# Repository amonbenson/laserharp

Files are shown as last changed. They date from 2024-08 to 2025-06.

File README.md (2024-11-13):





## Development Setup

### Backend

Setup a virtual environment and install the dependencies:
```bash
python3 -m venv .venv --system-site-packages
source .venv/bin/activate
pip install -r requirements.txt
```

Run the server in development mode:
```bash
source .venv/bin/activate
python -m laserharp.server
```

### Frontend

Install node js and yarn:
```bash
wget -qO- https://raw.githubusercontent.com/nvm-sh/nvm/v0.40.1/install.sh | bash
nvm install --lts
nvm use --lts
npm install -g yarn
```

Install all dependencies:
```bash
cd frontend
yarn install
```

Run the development server:
```bash
yarn dev
```

## Raspberry Pi Performance Improvements:

see https://wiki.linuxaudio.org/wiki/raspberrypi

```bash
for cpu in /sys/devices/system/cpu/cpu[0-9]*; do echo -n performance \
| sudo tee $cpu/cpufreq/scaling_governor; done
```

## Raspberry Pi Reduce Power Consumption

see https://www.jeffgeerling.com/blog/2023/reducing-raspberry-pi-5s-power-consumption-140x

```bash
# sudo rpi-eeprom-config -e
[all]
BOOT_UART=1
WAKE_ON_GPIO=0
POWER_OFF_ON_HALT=1
```

## Midi uart
- do a `rpi-update` to get the latest kernel firmware
- add to `/boot/firmware/config.txt`:
```
dtoverlay=uart2-pi5
dtoverlay=midi-uart2-pi5
```

## Power via GPIO header
http://blog.dddac.com/wp-content/uploads/Flash-RPi5-and-adding-5000mA-Line-tutorial.pdf

## Allow current user to shutdown
```bash
sudo chmod u+s /sbin/poweroff /sbin/reboot /sbin/shutdown
```

## Diode to Note Mapping

- Root note: C3 (midi note 48, one octave below middle C)
- Global transpose setting

- Modes:
    - **Pedal Harp**: For each note, choose one of:
        - flat
        - natural
        - sharp
    - **Custom Scale**:
        - each diode can be assigned to a specific midi note

- The harp is divided into three horizontal sections resulting in 3 different octave ranges

## Transmitted MIDI Messages

:heavy_check_mark: &ndash; Implemented<br>
:x: &ndash; Not implemented

### Note On :heavy_check_mark:

```
Laserharp -> Host: 0x90 <note> <velocity>
```
Sent when a laser is intercepted. The note value is determined by the diode and section that was intercepted. The velocity is fixed at 127.

### Note Off :heavy_check_mark:

```
Laserharp -> Host: 0x80 <note> <velocity>
```

Sent immediately after a laser was plucked. The velocity is fixed at 127.

### Pitch Bend :x:

```
Laserharp -> Host: 0xe0 <pitch_bend_msb> <pitch_bend_lsb>
```

Sent during interception when the hand is moved along the laser beam.

## Received MIDI Messages

:heavy_check_mark: &ndash; Implemented<br>
:x: &ndash; Not implemented

### Set Laser Brightness Directly (Note On / Note Off) :heavy_check_mark: (set all lasers :x:)

```
Host -> Laserharp: 0x80 <note> <velocity>
```

Turn off the laser corresponding to the note. A note value of 127 will turn off all lasers at once.

```
Host -> Laserharp: 0x90 <note> <velocity>
```

Turn on the laser corresponding to the note. A note value of 127 will turn on all lasers at once. The velocity determines the brightness of the laser.

The brightness is restored automatically after 1s. Note that interceptions will not be detected when the laser is turned off or too dim.

### Restore Laser Brightness (CC 102) :heavy_check_mark:

```
Host -> Laserharp: 0xb0 102 <value>
```

Restores the laser brightness to the previous value immediately. Value must be &ge; 64.

### Set Unplucked Laser Brightness (CC 103) :heavy_check_mark:

```
Host -> Laserharp: 0xb0 103 <brightness>
```

Set the brightness for unplucked lasers.

### Set Plucked Laser Brightness (CC 104) :heavy_check_mark:

```
Host -> Laserharp: 0xb0 104 <brightness>
```

Set the brightness when a laser is plucked.

### Set Muted Laser Brightness (CC 105) :heavy_check_mark:

```
Host -> Laserharp: 0xb0 105 <brightness>
```

Sets the brightness when a laser is muted.

### Set Pedal Position And Mutes (CC 110 - 116) :heavy_check_mark:

```
Host -> Laserharp: 0xb0 <pedal_cc> <position>
```

Sets the position and mute of a pedal.
The pedals are mapped as follows:

- CC 110 &ndash; C pedal
- CC 111 &ndash; D pedal
- CC 112 &ndash; E pedal
- CC 113 &ndash; F pedal
- CC 114 &ndash; G pedal
- CC 115 &ndash; A pedal
- CC 116 &ndash; B pedal

The value is divided into the ranges:

- 0 &ndash; 31 &ndash; muted
- 32 &ndash; 63 &ndash; lower position (sharp)
- 64 &ndash; 95 &ndash; middle position (natural)
- 96 &ndash; 127 &ndash; upper position (flat)

## IPC Protocol

:heavy_check_mark: &ndash; Implemented<br>
:x: &ndash; Not implemented

### USB Midi :x:

```
Bidirectional: 0x0N <byte0> <byte1> <byte2>
```

These packets are equivalent to the USB Midi Protocol with `CN = 1`.

### Din Midi :x:

```
Bidirectional: 0x1N <byte0> <byte1> <byte2>
```

_Note: With the current version, Din Midi is handled directly by the Raspberry Pi, so this message won't be used._

These packets are equivalent to the USB Midi Protocol with `CN = 1`.

### Set Brightness of a Single Laser :heavy_check_mark:

```
RPi -> STM: 0x80 <diode_index> <brightness> <fade_duration>
```

Set the brightness of a single laser diode. The fade duration is given in tenths of a second. E.g. a value of 20 will fade the laser to the new brightness over 2 seconds. A duration of 0 will set the brightness immediately.

### Set Brightness of All Lasers :heavy_check_mark:

```
RPi -> STM: 0x81 <brightness> <fade_duration> <unused>
```

Set the brightness of all laser diodes. The fade duration is given in tenths of a second. E.g. a value of 20 will fade the lasers to the new brightness over 2 seconds. A duration of 0 will set the brightness immediately.

### Get Brightness of a Single Laser :heavy_check_mark:

```
RPi -> STM: 0x82 <diode_index> <unused> <unused>
STM -> RPi: 0x82 <diode_index> <brightness> <unused>
```

### Play Animation :heavy_check_mark:

```
RPi -> STM: 0x83 <animation_id> <duration> <follow_action>
```

Play one of the predefined animations.

**Animation Ids**:<br>
0 &ndash; **Boot animation** &ndash; Played during powerup of the Raspberry Pi<br>
1 &ndash; **Flip animation** &ndash; Played when flipping the harp view<br>
2 &ndash; **Test animation** &ndash; Used for internal testing, alternates between diodes 4 and 5

**Duration**: Given in tenths of a second. E.g. a value of 20 will play the animation for 2 seconds.

**Follow Actions**:<br>
0 &ndash; **Loop** &ndash; Loop the animation indefinitely<br>
1 &ndash; **Freeze** &ndash; Play the animation once and stop on the last frame<br>
2 &ndash; **Off** &ndash; Play the animation once and stop with all lasers off<br>
3 &ndash; **Restore** &ndash; Play the animation once and restore the laser brightnesses

### Stop Animation :heavy_check_mark:

```
RPi -> STM: 0x84 <unused> <unused> <unused>
```

Stop the current animation from playing and execute the follow action immediately. If the follow action was set to 0 (loop indefinitely), the animation will stop and the lasers will remain in their current state.

### Calibration Button Pressed :heavy_check_mark:

```
STM -> RPi: 0x90 <state_0> <state_1> <state_2>
```

Sent when the calibration button is pressed. The states are given as follows:
0 &ndash; released<br>
1 &ndash; short press<br>
2 &ndash; long press

For example, if the button is short-pressed, then long-pressed, and then released, the states will be `0x01 0x02 0x00`.

### Get Voltage :heavy_check_mark:

```
RPi -> STM: 0x91 <00> <unused> <unused>
STM -> RPi: 0x91 <00> <voltage_int> <voltage_frac>
```

Returns the current voltage. Currently only the Laser Diode voltage (index 0) can be measured. The result is given as a decimal number with a resolution of 0.01V and can be calculated as follows:

```python
voltage = voltage_int + voltage_frac / 100
```

### Firmware Version Inquiry :heavy_check_mark:

```
RPi -> STM: 0xf0 <unused> <unused> <unused>
STM -> RPi: 0xf0 <major> <minor> <patch>
```

### Reboot STM :heavy_check_mark:

```
RPi -> STM: 0xf1 <unused> <unused> <unused>
```

### Enter Standby :heavy_check_mark:

```
RPi -> STM: 0xf2 <fade_delay> <fade_duration> <unused>
```

Starts by playing the boot animation, waits for the fade delay, and then fades the lasers to black over the fade duration. Both delay and duration are given in tenths of a second.

**Important: This is intended to be used when the harp is turned off. It will block any further IPC commands and the STM will not respond until it is power cycled.**

## TODO Software

### Pedal Mutes

- Each Pedal Switch should have a "mute" button. If a string is muted, its corresponding laser will be turned on very dimly and no sound will be produced for that string.

### Direct Laser Control

- The brightness of each laser should be directly controllable via Note On Messages.
- Velocity 1 will map to 0% brightness, velocity 127 will map to 100% brightness.
- Velocity 0 / Note Off will return to normal operation and use the internally calculated laser brightness
- If a laser is currently in "normal operation" mode, the color will be determined by the "unplucked", "plucked", and "muted" brightness settings.

### Section Mode / Section Transpose (formally Section Octave Spacing)

- Sections can be set to different modes.
    - Off &ndash; There are no different sections. Each laser will produce a single note.
    - Alterate &ndash; The upper section will play one semitone higher while the lower section will play one semitone lower.
    - Single Octave &ndash; The upper section will play one octave higher while the lower section will play one octave lower.
    - Double Octave &ndash; The upper section will play two octaves higher while the lower section will play two octaves lower.
- Internally, the section mode is stored as a number of semitones.
- This should also be controllable via a Control Change Message

### Global Transpose

- Instead of setting the root note, a fixed root note (e.g. C3) will be used and a global transpose setting will offset that root note.

### Direct Pedal/Mute Control

- Using Control Change Messages, the pedal position and mutes can be controlled.

### Predefined Scales

- Each predefined scale controls the pedal positions and mutes for each note.
- Can be selected using Bank Change Messages (CC 0).
- Additional custom scales can be defined and stored internally.

- For each scale, choose:
    - Pitch: `C C# D D# E F F# G G# A A# B`
    - Modes (see https://en.wikipedia.org/wiki/List_of_musical_scales_and_modes):
        - Lydian Dominant &ndash; `1 2 3 #4 5 6 b7`

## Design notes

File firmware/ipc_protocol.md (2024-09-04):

## Uses USB Midi internally

CN 0: DIN
CN 1: USB
CN 2: BLE
CN 8: Laser Brightness (note 127 = set all)

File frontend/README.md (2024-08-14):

# laserharp

This template should help get you started developing with Vue 3 in Vite.

## Recommended IDE Setup

[VSCode](https://code.visualstudio.com/) + [Volar](https://marketplace.visualstudio.com/items?itemName=Vue.volar) (and disable Vetur).

## Customize configuration

See [Vite Configuration Reference](https://vitejs.dev/config/).

## Project Setup

```sh
npm install
```

### Compile and Hot-Reload for Development

```sh
npm run dev
```

### Compile and Minify for Production

```sh
npm run build
```

### Lint with [ESLint](https://eslint.org/)

```sh
npm run lint
```

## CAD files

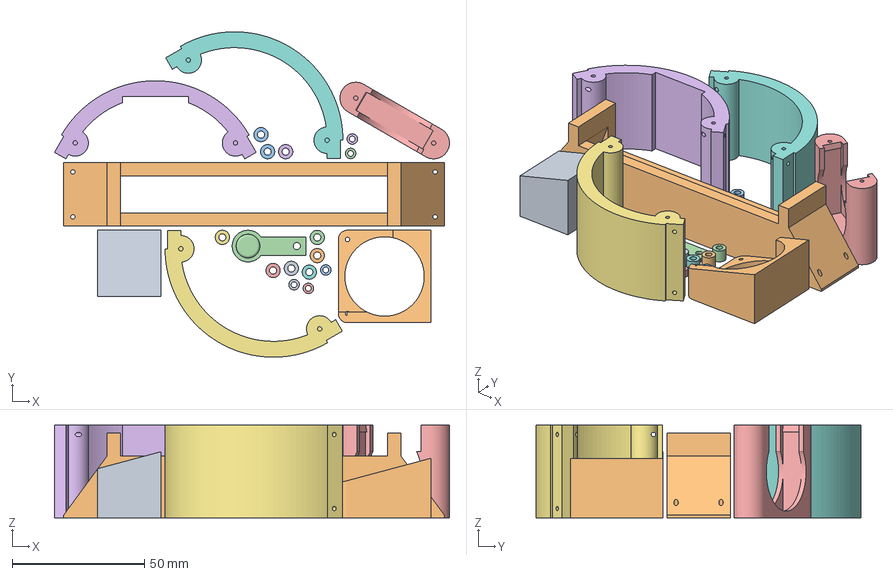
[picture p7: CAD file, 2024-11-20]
hardware/3dp/3dp_parts.3mf
149.4 x 123.1 x 35.0 mm
Small Spacer.3mf
Laser Cabinet.3mf
Large Spacer.3mf
Front Button.3mf
Fan Mount.3mf
Case Top.3mf
Case Right.3mf
Case Left.3mf
Camera Mount.3mf
Camera Cabinet.3mf
Large Spacer.3mf(1)
Large Spacer.3mf(2)
Large Spacer.3mf(3)
Large Spacer.3mf(4)
Large Spacer.3mf(5)
Large Spacer.3mf(6)
Large Spacer.3mf(7)
Large Spacer.3mf(8)
Small Spacer.3mf(1)
Small Spacer.3mf(2)
Small Spacer.3mf(3)
Small Spacer.3mf(4)

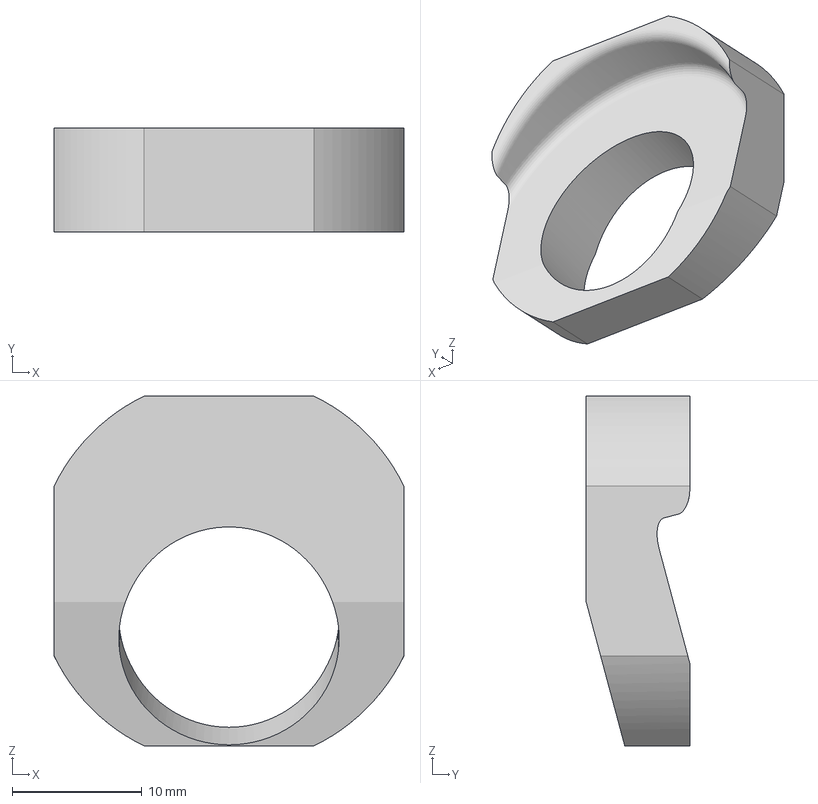
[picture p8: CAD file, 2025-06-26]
hardware/3dp/jlc3dp/LensMount.3mf
27.0 x 8.00 x 27.0 mm

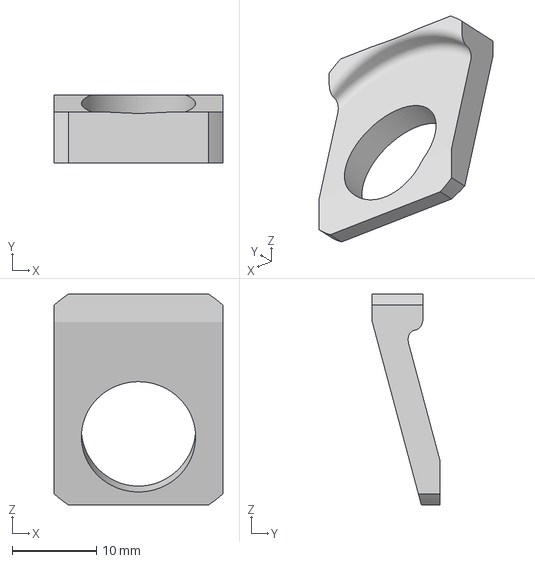
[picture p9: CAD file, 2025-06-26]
hardware/fusion360/Export/3D Printing/Lens Mount.3mf
20.0 x 8.00 x 25.0 mm

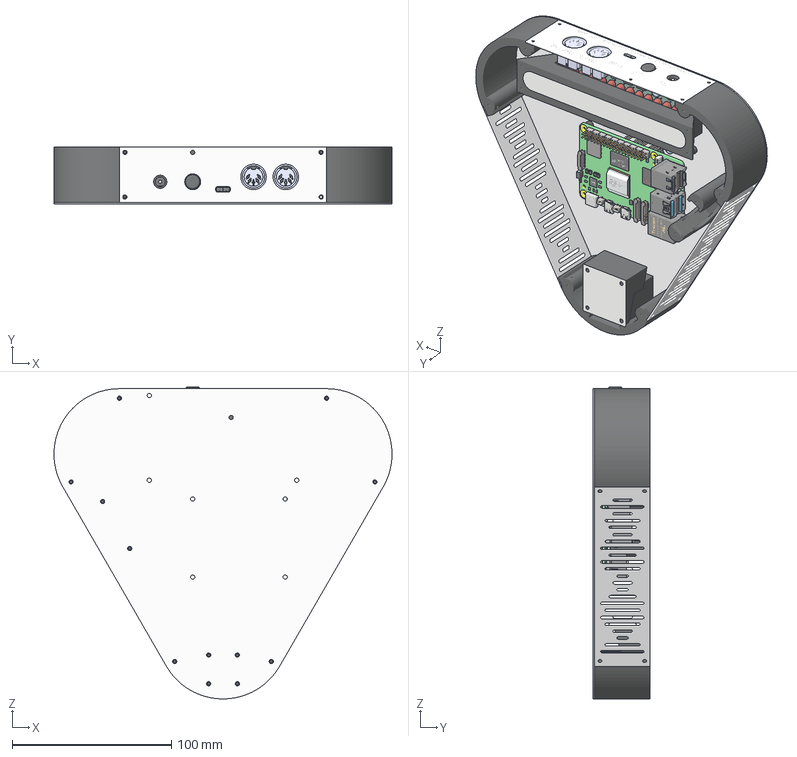
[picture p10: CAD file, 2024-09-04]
hardware/fusion360/Export/Laserharp Frameless 3DP Parts.3mf
212.0 x 36.0 x 195.6 mm
Bottom Plate
Camera Cabinet
Camera Cover
Camera Mount
Case Left
Case Right
Case Top
Fan Mount
Front Button
Front Plate
Laser Cabinet
Laser Cover
Left Side Panel
Right Side Panel
Spacer (1)
Spacer (10)
Spacer (11)
Spacer (2)
Spacer (3)
Spacer (4)
Spacer (5)
Spacer (6)
Spacer (7)
Spacer (8)
Spacer (9)
Spacer

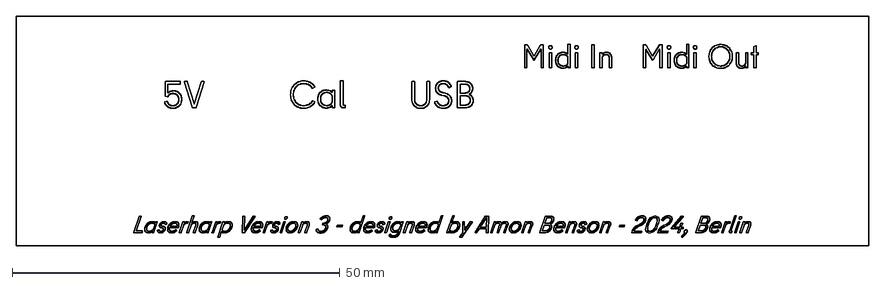
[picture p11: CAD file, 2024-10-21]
hardware/fusion360/Export/Sheet Metal/Engravings.dxf
130.0 x 35.0 mm

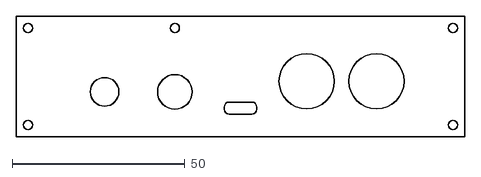
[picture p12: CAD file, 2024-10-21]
hardware/fusion360/Export/Sheet Metal/Fabrication/LH_Front_Outlines.dxf
130.0 x 35.0

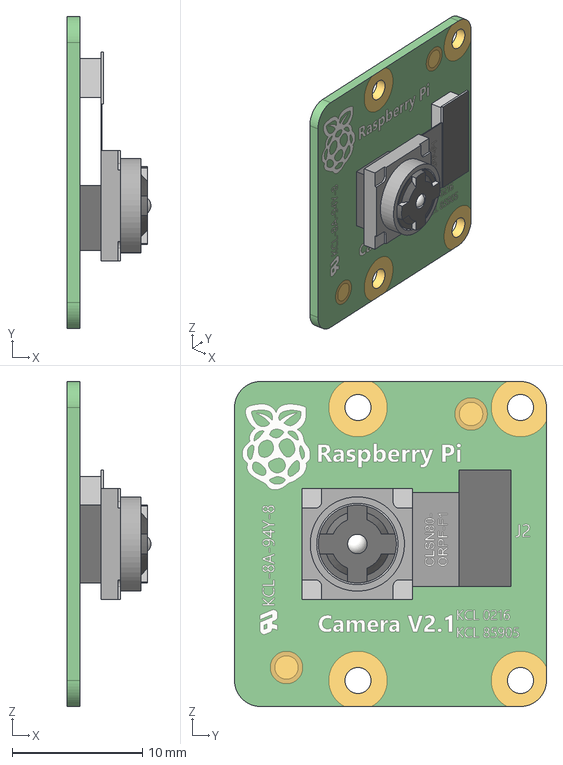
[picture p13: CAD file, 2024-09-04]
hardware/fusion360/PCB Models/Cam V2.1 v1.step
6.45 x 24.0 x 25.0 mm

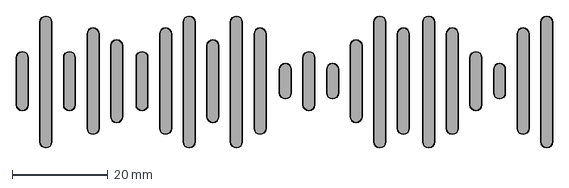
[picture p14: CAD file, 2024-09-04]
hardware/waveform_artwork.dxf
112.2 x 27.5 mm

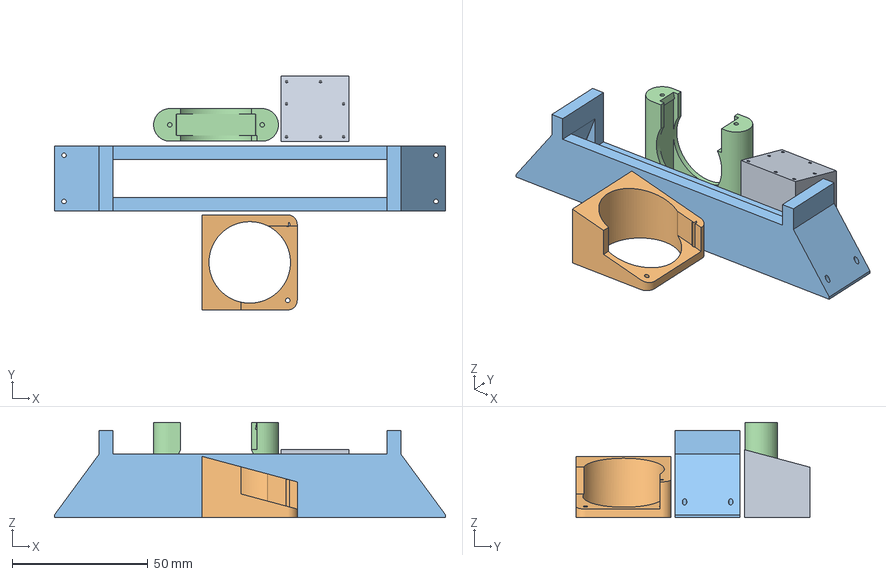
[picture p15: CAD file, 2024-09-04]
hardware/3dp/Cura_Mounts.3mf
144.0 x 86.1 x 35.0 mm
Camera Mount.3mf
Camera Cabinet.3mf
Laser Cabinet.3mf
Fan Mount.3mf

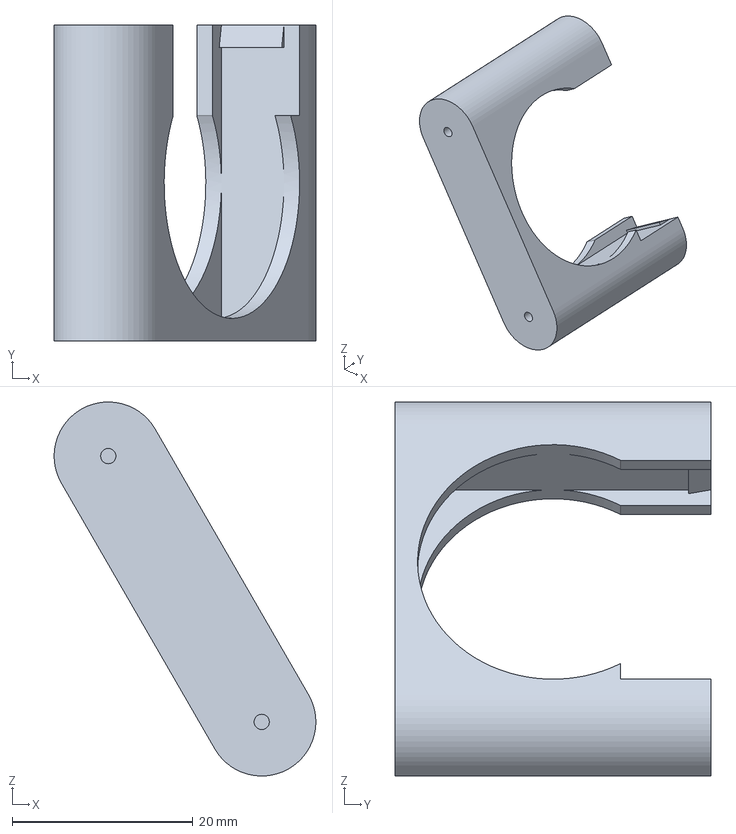
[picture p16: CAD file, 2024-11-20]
hardware/3dp/jlc3dp/FanMount.3mf
29.0 x 35.0 x 41.4 mm

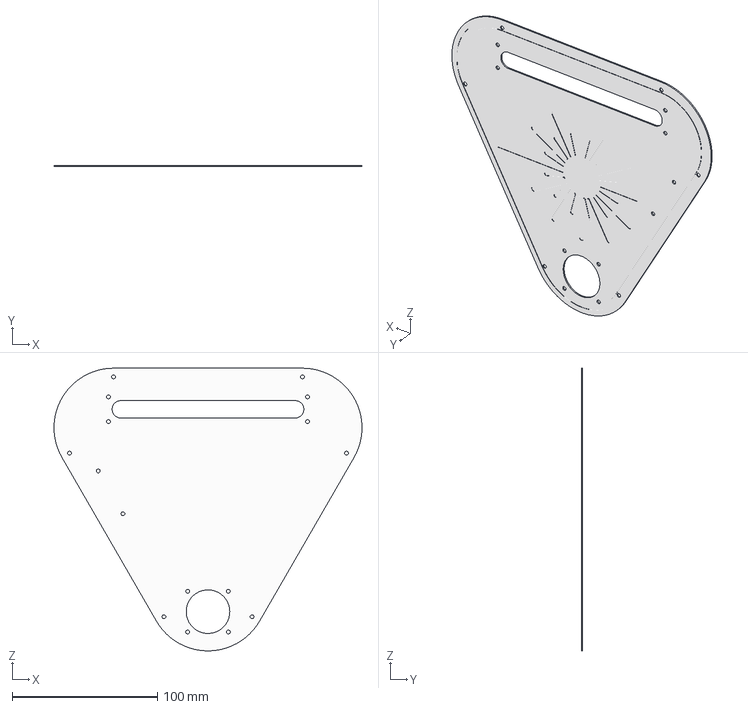
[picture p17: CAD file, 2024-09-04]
hardware/fusion360/Export/3D Printing/Top Plate.3mf
212.0 x 1.00 x 194.5 mm

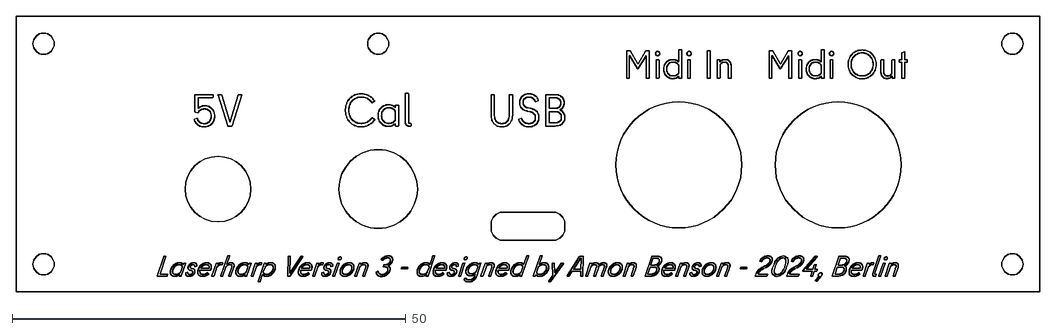
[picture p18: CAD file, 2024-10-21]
hardware/fusion360/Export/Sheet Metal/Fabrication/LH_Front.dxf
130.0 x 35.0

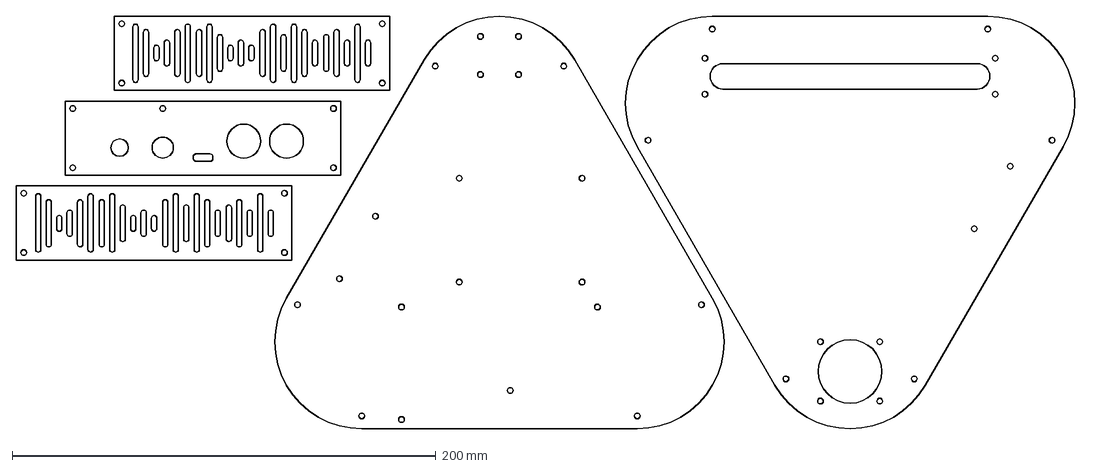
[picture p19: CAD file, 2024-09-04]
hardware/fusion360/Export/Sheet Metal/Outlines.dxf
501.2 x 194.6 mm

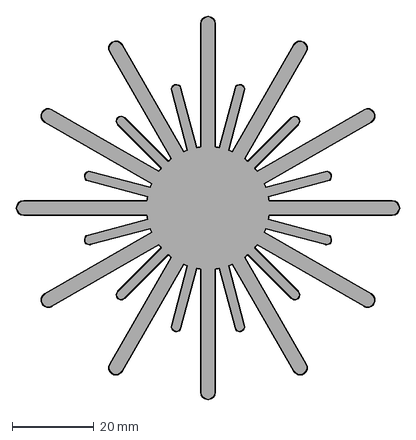
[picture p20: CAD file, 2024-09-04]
hardware/laser_artwork.dxf
93.5 x 93.5 mm

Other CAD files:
hardware/3dp/Cura_Top_Plate.3mf
hardware/3dp/jlc3dp/CameraCabinet.3mf
hardware/fusion360/Export/3D Printing/Front Button.3mf
hardware/fusion360/Export/Sheet Metal/Fabrication/LH_Left.dxf
hardware/3dp/Cura_Bottom_Plate.3mf
hardware/3dp/Cura_Case_And_Button.3mf
hardware/3dp/Cura_Panels.3mf
hardware/3dp/Cura_Spacers.3mf
hardware/3dp/jlc3dp/CameraMount.3mf
hardware/3dp/jlc3dp/CaseLR_x2.3mf
hardware/3dp/jlc3dp/CaseTop.3mf
hardware/3dp/jlc3dp/FrontButton.3mf
hardware/3dp/jlc3dp/LargeSpacer_x9.3mf
hardware/3dp/jlc3dp/LaserCabinet.3mf
hardware/3dp/jlc3dp/SmallSpacer_x5.3mf
hardware/Top Plate.dxf
hardware/fusion360/Export/3D Printing/Bottom Plate.3mf
hardware/fusion360/Export/3D Printing/Camera Cabinet.3mf
hardware/fusion360/Export/3D Printing/Camera Mount.3mf
hardware/fusion360/Export/3D Printing/Case Left.3mf
hardware/fusion360/Export/3D Printing/Case Right.3mf
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

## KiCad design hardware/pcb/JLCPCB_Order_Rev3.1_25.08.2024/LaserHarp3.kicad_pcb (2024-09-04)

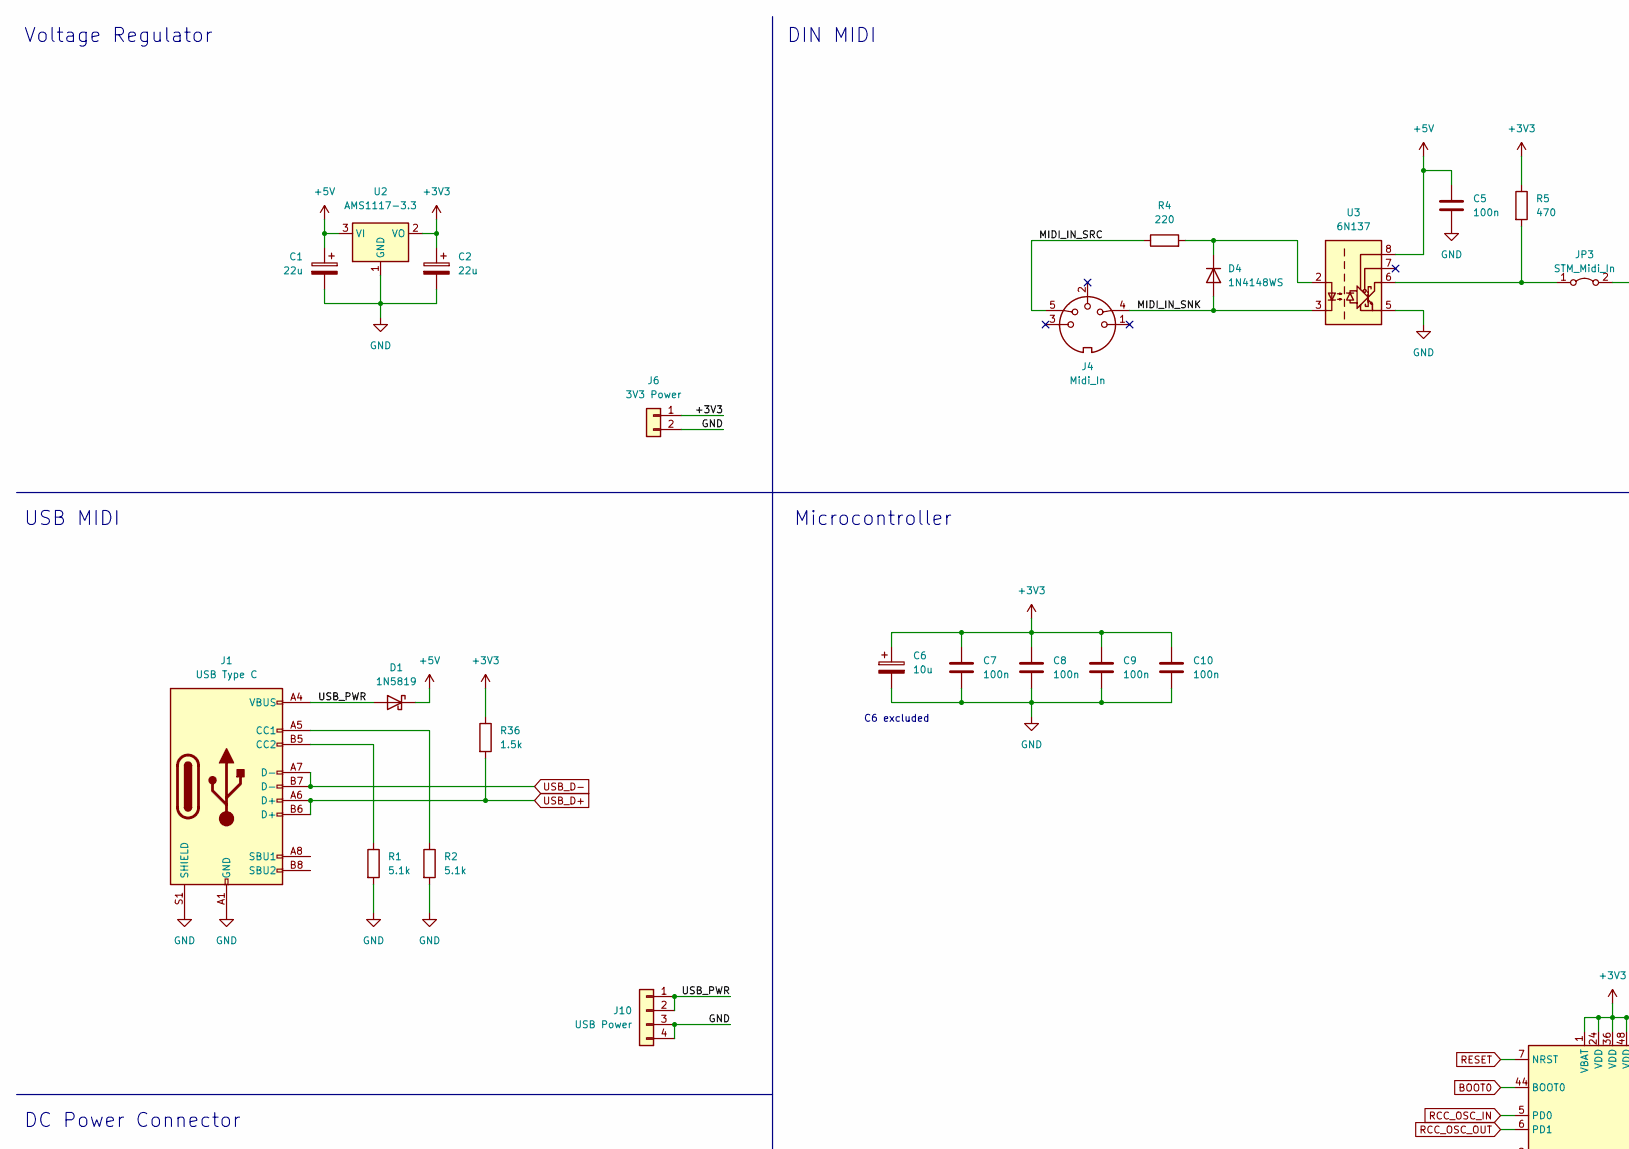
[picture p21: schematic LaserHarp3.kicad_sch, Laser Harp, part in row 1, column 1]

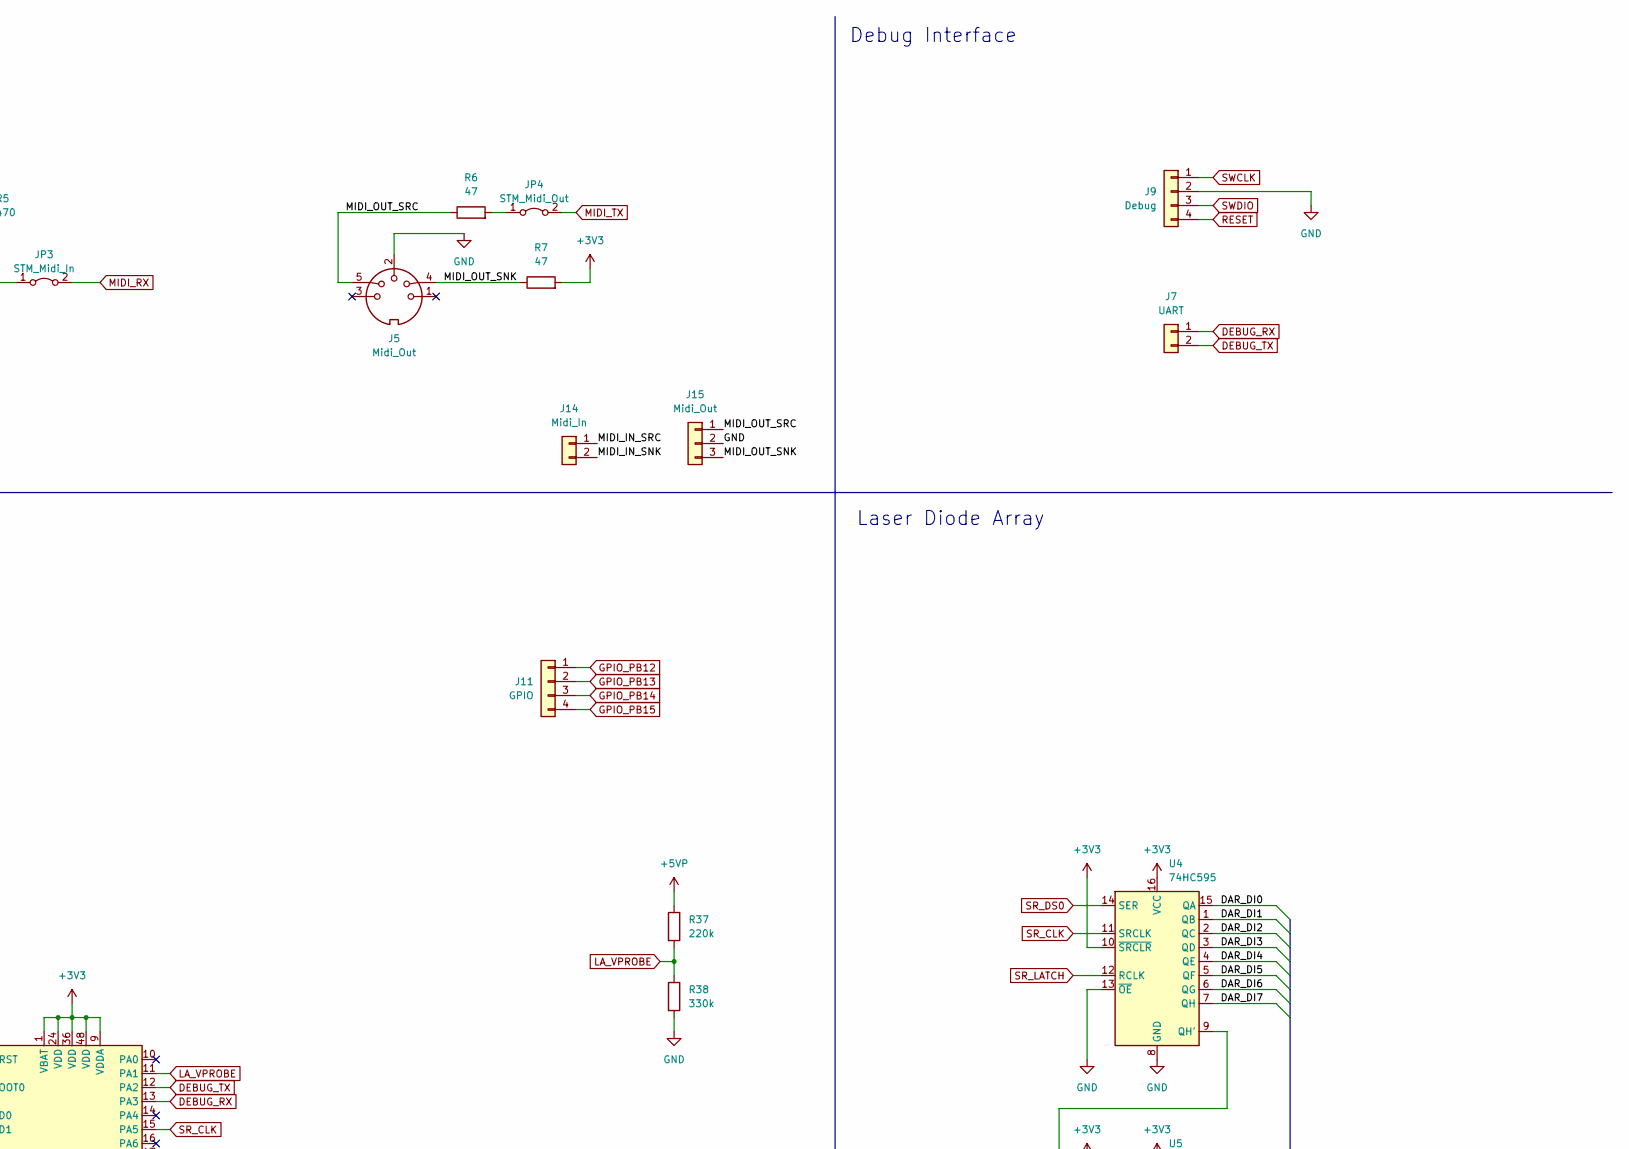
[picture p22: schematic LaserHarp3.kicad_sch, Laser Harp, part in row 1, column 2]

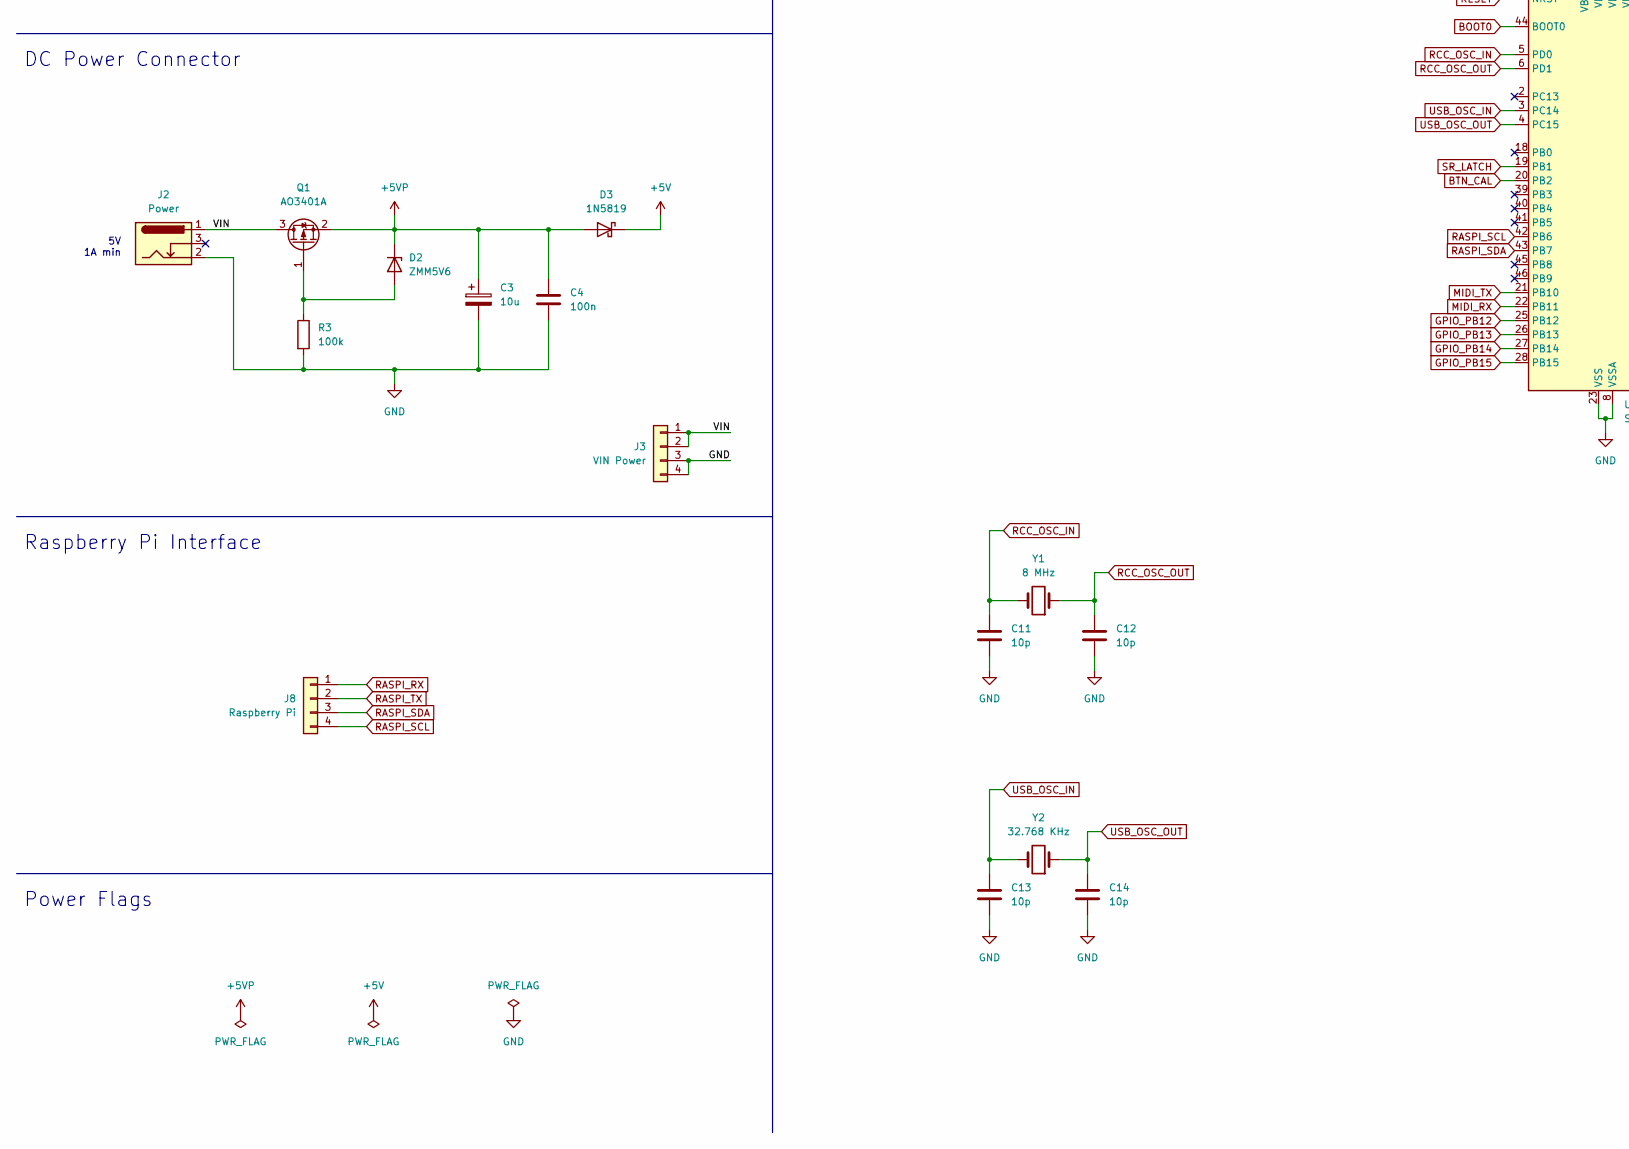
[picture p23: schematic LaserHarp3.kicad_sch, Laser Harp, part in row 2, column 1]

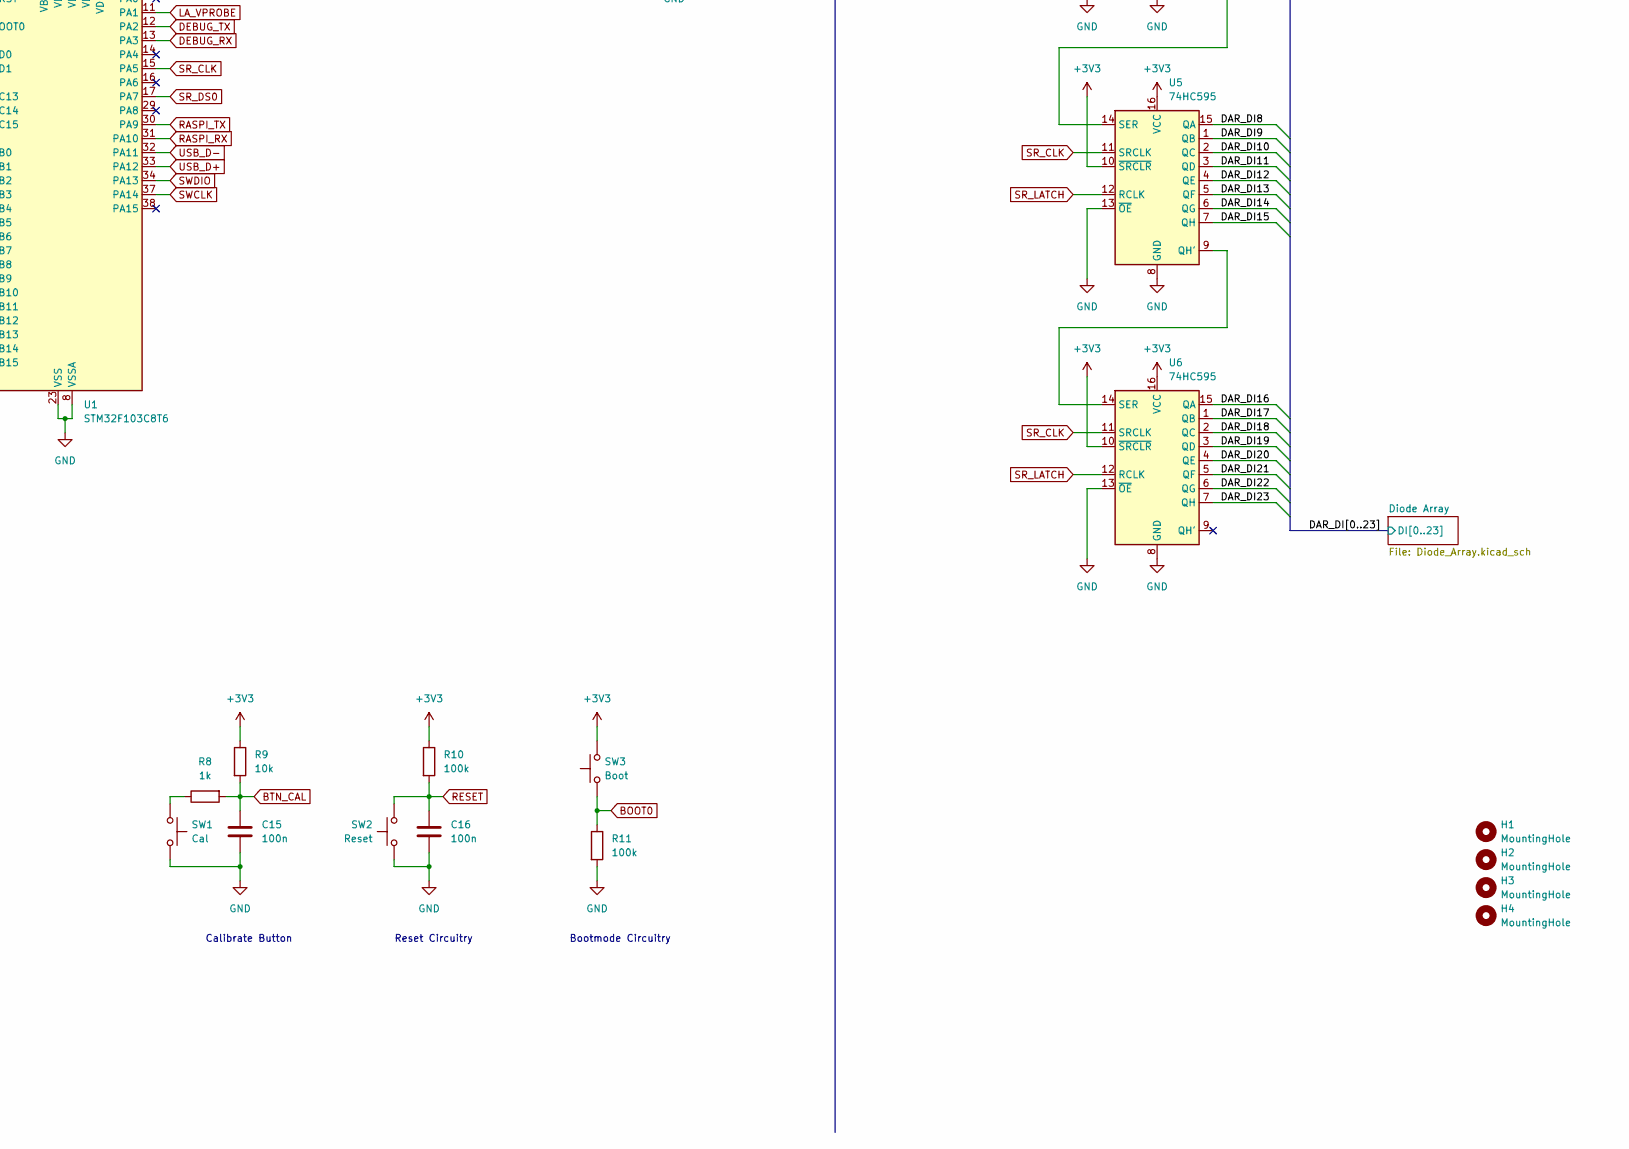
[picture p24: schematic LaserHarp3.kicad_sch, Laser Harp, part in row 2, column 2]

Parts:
C1, C2: 22u; C_Radial_D6.3mm_H5.0mm_P2.50mm
C3, C6: 10u; C_Radial_D6.3mm_H5.0mm_P2.50mm
C4, C5, C7, C8, C9, C10, C15, C16: 100n; C_0603_1608Metric; LCSC C14663
C11, C12, C13, C14: 10p; C_0603_1608Metric; LCSC C1634
D1, D3: 1N5819; D_SOD-323; LCSC C191023
D2: ZMM5V6; D_MiniMELF; LCSC C5345993
D4: 1N4148WS; D_SOD-323; LCSC C2128
H1, H2, H3, H4: MountingHole; MountingHole_2.7mm
J1: USB Type C; USB_C_Receptacle_Palconn_UTC16-G; LCSC C2927038
J2: Power; BarrelJack_CUI_PJ-102AH_Horizontal
J3: VIN Power; PinHeader_1x04_P2.54mm_Vertical
J4: Midi_In; din-5
J5: Midi_Out; din-5
J6: 3V3 Power; PinHeader_1x02_P2.54mm_Vertical
J7: UART; PinHeader_1x02_P2.54mm_Vertical
J8: Raspberry Pi; PinHeader_1x04_P2.54mm_Vertical
J9: Debug; PinHeader_1x04_P2.54mm_Vertical
J10: USB Power; PinHeader_1x04_P2.54mm_Vertical
J11: GPIO; PinHeader_2x02_P2.54mm_Vertical
J14: Midi_In; SolderWire-0.1sqmm_1x02_P3.6mm_D0.4mm_OD1mm
J15: Midi_Out; SolderWire-0.1sqmm_1x03_P3.6mm_D0.4mm_OD1mm
JP3: STM_Midi_In; PinHeader_1x02_P2.54mm_Vertical
JP4: STM_Midi_Out; PinHeader_1x02_P2.54mm_Vertical
Q1: AO3401A; SOT-23; LCSC C15127
R1, R2: 5.1k; R_0603_1608Metric; LCSC C23186
R3, R10, R11: 100k; R_0603_1608Metric; LCSC C25803
R4: 220; R_0603_1608Metric; LCSC C22962
R5: 470; R_0603_1608Metric; LCSC C23179
R6, R7: 47; R_0603_1608Metric; LCSC C23182
R8: 1k; R_0603_1608Metric; LCSC C21190
R9: 10k; R_0603_1608Metric; LCSC C25804
R36: 1.5k; R_0603_1608Metric
R37: 220k; R_0603_1608Metric; LCSC C22961
R38: 330k; R_0603_1608Metric; LCSC C23137
SW1: Cal; SW_Tactile_SPST_Angled_PTS645Vx39-2LFS
SW2: Reset; SW_PUSH_6mm
SW3: Boot; SW_PUSH_6mm
U1: STM32F103C8T6; LQFP-48_7x7mm_P0.5mm; LCSC C8734
U2: AMS1117-3.3; SOT-223-3_TabPin2; LCSC C6186
U3: 6N137; SSO-8_6.7x9.8mm_P2.54mm_Clearance8mm; LCSC C110020
U4, U5, U6: 74HC595; SO-16_3.9x9.9mm_P1.27mm; LCSC C5947
Y1: 8 MHz; Crystal_SMD_HC49-SD; LCSC C12674
Y2: 32.768 KHz; Crystal_SMD_3215-2Pin_3.2x1.5mm; LCSC C32346

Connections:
+3V3: C2.1, C6.1, C7.1, C8.1, C9.1, C10.1, J6.1, R5.1, R7.2, R9.1, R10.1, R36.1, SW3.2, U1.1 (VBAT), U1.9 (VDDA), U1.24 (VDD), U1.36 (VDD), U1.48 (VDD), U2.2 (VO), U4.10 (~SRCLR), U4.16 (VCC), U5.10 (~SRCLR), U5.16 (VCC), U6.10 (~SRCLR), U6.16 (VCC)
+5V: C1.1, C5.1, D1.1 (K), D3.1 (K), U2.3 (VI), U3.8 (VCC)
+5VP: C3.1, C4.1, D2.1 (K), D3.2 (A), Q1.2 (S), R37.1; also elsewhere on the board
/DAR_DI0: U4.15 (QA); also elsewhere on the board
/DAR_DI1: U4.1 (QB); also elsewhere on the board
/DAR_DI2: U4.2 (QC); also elsewhere on the board
/DAR_DI3: U4.3 (QD); also elsewhere on the board
/DAR_DI4: U4.4 (QE); also elsewhere on the board
/DAR_DI5: U4.5 (QF); also elsewhere on the board
/DAR_DI6: U4.6 (QG); also elsewhere on the board
/DAR_DI7: U4.7 (QH); also elsewhere on the board
/DAR_DI8: U5.15 (QA); also elsewhere on the board
/DAR_DI9: U5.1 (QB); also elsewhere on the board
/DAR_DI10: U5.2 (QC); also elsewhere on the board
/DAR_DI11: U5.3 (QD); also elsewhere on the board
/DAR_DI12: U5.4 (QE); also elsewhere on the board
/DAR_DI13: U5.5 (QF); also elsewhere on the board
/DAR_DI14: U5.6 (QG); also elsewhere on the board
/DAR_DI15: U5.7 (QH); also elsewhere on the board
/DAR_DI16: U6.15 (QA); also elsewhere on the board
/DAR_DI17: U6.1 (QB); also elsewhere on the board
/DAR_DI18: U6.2 (QC); also elsewhere on the board
/DAR_DI19: U6.3 (QD); also elsewhere on the board
/DAR_DI20: U6.4 (QE); also elsewhere on the board
/DAR_DI21: U6.5 (QF); also elsewhere on the board
/DAR_DI22: U6.6 (QG); also elsewhere on the board
/DAR_DI23: U6.7 (QH); also elsewhere on the board
/MIDI_IN_SNK: D4.2 (A), J4.4, J14.2, U3.3 (C)
/MIDI_IN_SRC: J4.5, J14.1, R4.1
/MIDI_OUT_SNK: J5.4, J15.3, R7.1
/MIDI_OUT_SRC: J5.5, J15.1, R6.1
/USB_PWR: D1.2 (A), J1.A4 (VBUS), J1.A9 (VBUS), J1.B4 (VBUS), J1.B9 (VBUS), J10.1, J10.2
/VIN: J2.1, J3.1, J3.2, Q1.3 (D)
BOOT0: R11.1, SW3.1, U1.44 (BOOT0)
BTN_CAL: C15.1, R8.2, R9.2, U1.20 (PB2)
DEBUG_RX: J7.1, U1.13 (PA3)
DEBUG_TX: J7.2, U1.12 (PA2)
GND: C1.2, C2.2, C3.2, C4.2, C5.2, C6.2, C7.2, C8.2, C9.2, C10.2, C11.2, C12.2, C13.2, C14.2, C15.2, C16.2, J1.A1 (GND), J1.A12 (GND), J1.B1 (GND), J1.B12 (GND), J1.S1 (SHIELD), J2.2, J3.3, J3.4, J5.2, J6.2, J9.2, J10.3, J10.4, J15.2, R1.2, R2.2, R3.2, R11.2, R38.2, SW1.2, SW2.1, U1.8 (VSSA), U1.23 (VSS), U1.35 (VSS), U1.47 (VSS), U2.1 (GND), U3.5 (GND), U4.8 (GND), U4.13 (~OE), U5.8 (GND), U5.13 (~OE), U6.8 (GND), U6.13 (~OE); also elsewhere on the board
GPIO_PB12: J11.1, U1.25 (PB12)
GPIO_PB13: J11.2, U1.26 (PB13)
GPIO_PB14: J11.3, U1.27 (PB14)
GPIO_PB15: J11.4, U1.28 (PB15)
LA_VPROBE: R37.2, R38.1, U1.11 (PA1)
MIDI_RX: JP3.2 (B), U1.22 (PB11)
MIDI_TX: JP4.2 (B), U1.21 (PB10)
unnamed: D2.2 (A), Q1.1 (G), R3.1
unnamed: D4.1 (K), R4.2, U3.2 (A)
unnamed: J1.A5 (CC1), R2.1
unnamed: J1.B5 (CC2), R1.1
unnamed: JP3.1 (A), R5.2, U3.6 (VO)
unnamed: JP4.1 (A), R6.2
unnamed: R8.1, SW1.1
unnamed: U4.9 (QH'), U5.14 (SER)
unnamed: U5.9 (QH'), U6.14 (SER)
RASPI_RX: J8.1, U1.31 (PA10)
RASPI_SCL: J8.4, U1.42 (PB6)
RASPI_SDA: J8.3, U1.43 (PB7)
RASPI_TX: J8.2, U1.30 (PA9)
RCC_OSC_IN: C11.1, U1.5 (PD0), Y1.2
RCC_OSC_OUT: C12.1, U1.6 (PD1), Y1.1
RESET: C16.1, J9.4, R10.2, SW2.2, U1.7 (NRST)
SR_CLK: U1.15 (PA5), U4.11 (SRCLK), U5.11 (SRCLK), U6.11 (SRCLK)
SR_DS0: U1.17 (PA7), U4.14 (SER)
SR_LATCH: U1.19 (PB1), U4.12 (RCLK), U5.12 (RCLK), U6.12 (RCLK)
SWCLK: J9.1, U1.37 (PA14)
SWDIO: J9.3, U1.34 (PA13)
USB_D+: J1.A6 (D+), J1.B6 (D+), R36.2, U1.33 (PA12)
USB_D-: J1.A7 (D-), J1.B7 (D-), U1.32 (PA11)
USB_OSC_IN: C13.1, U1.3 (PC14), Y2.2
USB_OSC_OUT: C14.1, U1.4 (PC15), Y2.1

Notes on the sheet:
Debug Interface
Microcontroller
5V 1A min
DIN MIDI
C6 excluded
Raspberry Pi Interface
Calibrate Button
Bootmode Circuitry
Laser Diode Array
Reset Circuitry
USB MIDI
Power Flags
Voltage Regulator
DC Power Connector

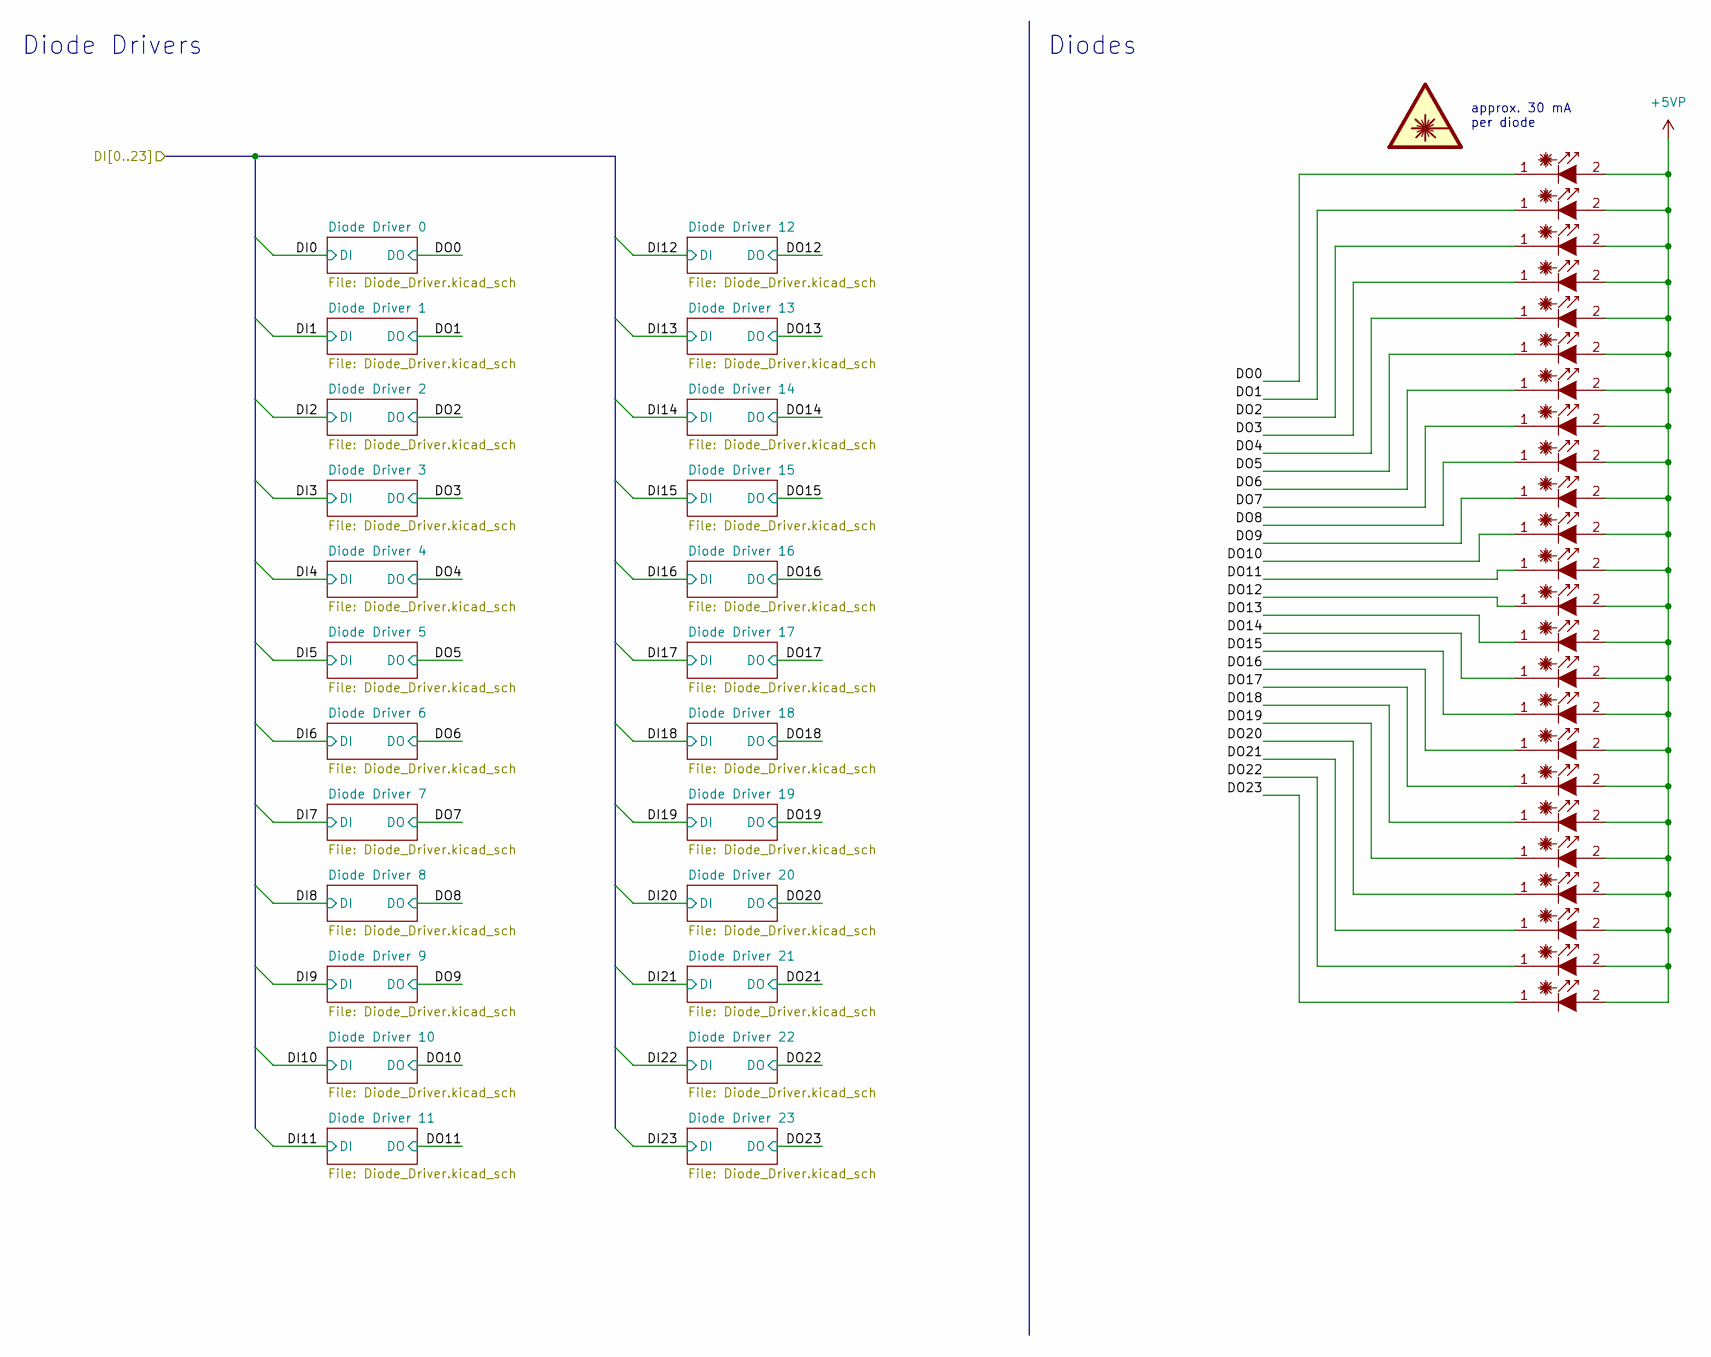
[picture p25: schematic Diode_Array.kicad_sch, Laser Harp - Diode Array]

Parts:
LD1, LD2, LD3, LD4, LD5, LD6, LD7, LD8, LD9, LD10, LD11, LD12, LD13, LD14, LD15, LD16, LD17, LD18, LD19, LD20, LD21, LD22, LD23, LD24: Laser_Diode; LED_D5.0mm

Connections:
+5VP: LD1.2 (A), LD2.2 (A), LD3.2 (A), LD4.2 (A), LD5.2 (A), LD6.2 (A), LD7.2 (A), LD8.2 (A), LD9.2 (A), LD10.2 (A), LD11.2 (A), LD12.2 (A), LD13.2 (A), LD14.2 (A), LD15.2 (A), LD16.2 (A), LD17.2 (A), LD18.2 (A), LD19.2 (A), LD20.2 (A), LD21.2 (A), LD22.2 (A), LD23.2 (A), LD24.2 (A); also elsewhere on the board
/Diode Array/DO0: LD1.1 (C); also elsewhere on the board
/Diode Array/DO1: LD2.1 (C); also elsewhere on the board
/Diode Array/DO2: LD3.1 (C); also elsewhere on the board
/Diode Array/DO3: LD4.1 (C); also elsewhere on the board
/Diode Array/DO4: LD5.1 (C); also elsewhere on the board
/Diode Array/DO5: LD6.1 (C); also elsewhere on the board
/Diode Array/DO6: LD7.1 (C); also elsewhere on the board
/Diode Array/DO7: LD8.1 (C); also elsewhere on the board
/Diode Array/DO8: LD9.1 (C); also elsewhere on the board
/Diode Array/DO9: LD10.1 (C); also elsewhere on the board
/Diode Array/DO10: LD11.1 (C); also elsewhere on the board
/Diode Array/DO11: LD12.1 (C); also elsewhere on the board
/Diode Array/DO12: LD13.1 (C); also elsewhere on the board
/Diode Array/DO13: LD14.1 (C); also elsewhere on the board
/Diode Array/DO14: LD15.1 (C); also elsewhere on the board
/Diode Array/DO15: LD16.1 (C); also elsewhere on the board
/Diode Array/DO16: LD17.1 (C); also elsewhere on the board
/Diode Array/DO17: LD18.1 (C); also elsewhere on the board
/Diode Array/DO18: LD19.1 (C); also elsewhere on the board
/Diode Array/DO19: LD20.1 (C); also elsewhere on the board
/Diode Array/DO20: LD21.1 (C); also elsewhere on the board
/Diode Array/DO21: LD22.1 (C); also elsewhere on the board
/Diode Array/DO22: LD23.1 (C); also elsewhere on the board
/Diode Array/DO23: LD24.1 (C); also elsewhere on the board

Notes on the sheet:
Diodes
Diode Drivers
approx. 30 mA per diode

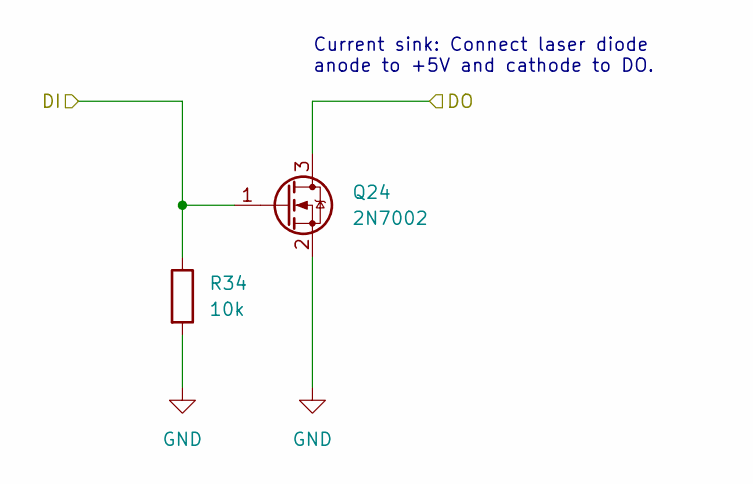
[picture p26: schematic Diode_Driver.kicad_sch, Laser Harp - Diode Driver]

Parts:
Q24: 2N7002; SOT-23; LCSC C8545
R34: 10k; R_0603_1608Metric; LCSC C25804

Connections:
/DAR_DI22: Q24.1 (G), R34.1; also elsewhere on the board
/Diode Array/DO22: Q24.3 (D); also elsewhere on the board
GND: Q24.2 (S), R34.2; also elsewhere on the board

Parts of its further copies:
Q2, Q3, Q4, Q5, Q6, Q7, Q8, Q9, Q10, Q11, Q12, Q13, Q14, Q15, Q16, Q17, Q18, Q19, Q20, Q21, Q22, Q23, Q25: 2N7002; SOT-23; LCSC C8545
R12, R13, R14, R15, R16, R17, R18, R19, R20, R21, R22, R23, R24, R25, R26, R27, R28, R29, R30, R31, R32, R33, R35: 10k; R_0603_1608Metric; LCSC C25804

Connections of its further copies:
/DAR_DI0: Q2.1 (G), R12.1; also elsewhere on the board
/DAR_DI1: Q3.1 (G), R13.1; also elsewhere on the board
/DAR_DI2: Q4.1 (G), R14.1; also elsewhere on the board
/DAR_DI3: Q5.1 (G), R15.1; also elsewhere on the board
/DAR_DI4: Q6.1 (G), R16.1; also elsewhere on the board
/DAR_DI5: Q7.1 (G), R17.1; also elsewhere on the board
/DAR_DI6: Q8.1 (G), R18.1; also elsewhere on the board
/DAR_DI7: Q9.1 (G), R19.1; also elsewhere on the board
/DAR_DI8: Q10.1 (G), R20.1; also elsewhere on the board
/DAR_DI9: Q11.1 (G), R21.1; also elsewhere on the board
/DAR_DI10: Q12.1 (G), R22.1; also elsewhere on the board
/DAR_DI11: Q13.1 (G), R23.1; also elsewhere on the board
/DAR_DI12: Q14.1 (G), R24.1; also elsewhere on the board
/DAR_DI13: Q15.1 (G), R25.1; also elsewhere on the board
/DAR_DI14: Q16.1 (G), R26.1; also elsewhere on the board
/DAR_DI15: Q17.1 (G), R27.1; also elsewhere on the board
/DAR_DI16: Q18.1 (G), R28.1; also elsewhere on the board
/DAR_DI17: Q19.1 (G), R29.1; also elsewhere on the board
/DAR_DI18: Q20.1 (G), R30.1; also elsewhere on the board
/DAR_DI19: Q21.1 (G), R31.1; also elsewhere on the board
/DAR_DI20: Q22.1 (G), R32.1; also elsewhere on the board
/DAR_DI21: Q23.1 (G), R33.1; also elsewhere on the board
/DAR_DI23: Q25.1 (G), R35.1; also elsewhere on the board
/Diode Array/DO0: Q2.3 (D); also elsewhere on the board
/Diode Array/DO1: Q3.3 (D); also elsewhere on the board
/Diode Array/DO2: Q4.3 (D); also elsewhere on the board
/Diode Array/DO3: Q5.3 (D); also elsewhere on the board
/Diode Array/DO4: Q6.3 (D); also elsewhere on the board
/Diode Array/DO5: Q7.3 (D); also elsewhere on the board
/Diode Array/DO6: Q8.3 (D); also elsewhere on the board
/Diode Array/DO7: Q9.3 (D); also elsewhere on the board
/Diode Array/DO8: Q10.3 (D); also elsewhere on the board
/Diode Array/DO9: Q11.3 (D); also elsewhere on the board
/Diode Array/DO10: Q12.3 (D); also elsewhere on the board
/Diode Array/DO11: Q13.3 (D); also elsewhere on the board
/Diode Array/DO12: Q14.3 (D); also elsewhere on the board
/Diode Array/DO13: Q15.3 (D); also elsewhere on the board
/Diode Array/DO14: Q16.3 (D); also elsewhere on the board
/Diode Array/DO15: Q17.3 (D); also elsewhere on the board
/Diode Array/DO16: Q18.3 (D); also elsewhere on the board
/Diode Array/DO17: Q19.3 (D); also elsewhere on the board
/Diode Array/DO18: Q20.3 (D); also elsewhere on the board
/Diode Array/DO19: Q21.3 (D); also elsewhere on the board
/Diode Array/DO20: Q22.3 (D); also elsewhere on the board
/Diode Array/DO21: Q23.3 (D); also elsewhere on the board
/Diode Array/DO23: Q25.3 (D); also elsewhere on the board
GND: Q2.2 (S), Q3.2 (S), Q4.2 (S), Q5.2 (S), Q6.2 (S), Q7.2 (S), Q8.2 (S), Q9.2 (S), Q10.2 (S), Q11.2 (S), Q12.2 (S), Q13.2 (S), Q14.2 (S), Q15.2 (S), Q16.2 (S), Q17.2 (S), Q18.2 (S), Q19.2 (S), Q20.2 (S), Q21.2 (S), Q22.2 (S), Q23.2 (S), Q25.2 (S), R12.2, R13.2, R14.2, R15.2, R16.2, R17.2, R18.2, R19.2, R20.2, R21.2, R22.2, R23.2, R24.2, R25.2, R26.2, R27.2, R28.2, R29.2, R30.2, R31.2, R32.2, R33.2, R35.2; also elsewhere on the board

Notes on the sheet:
Current sink: Connect laser diode anode to +5V and cathode to DO.

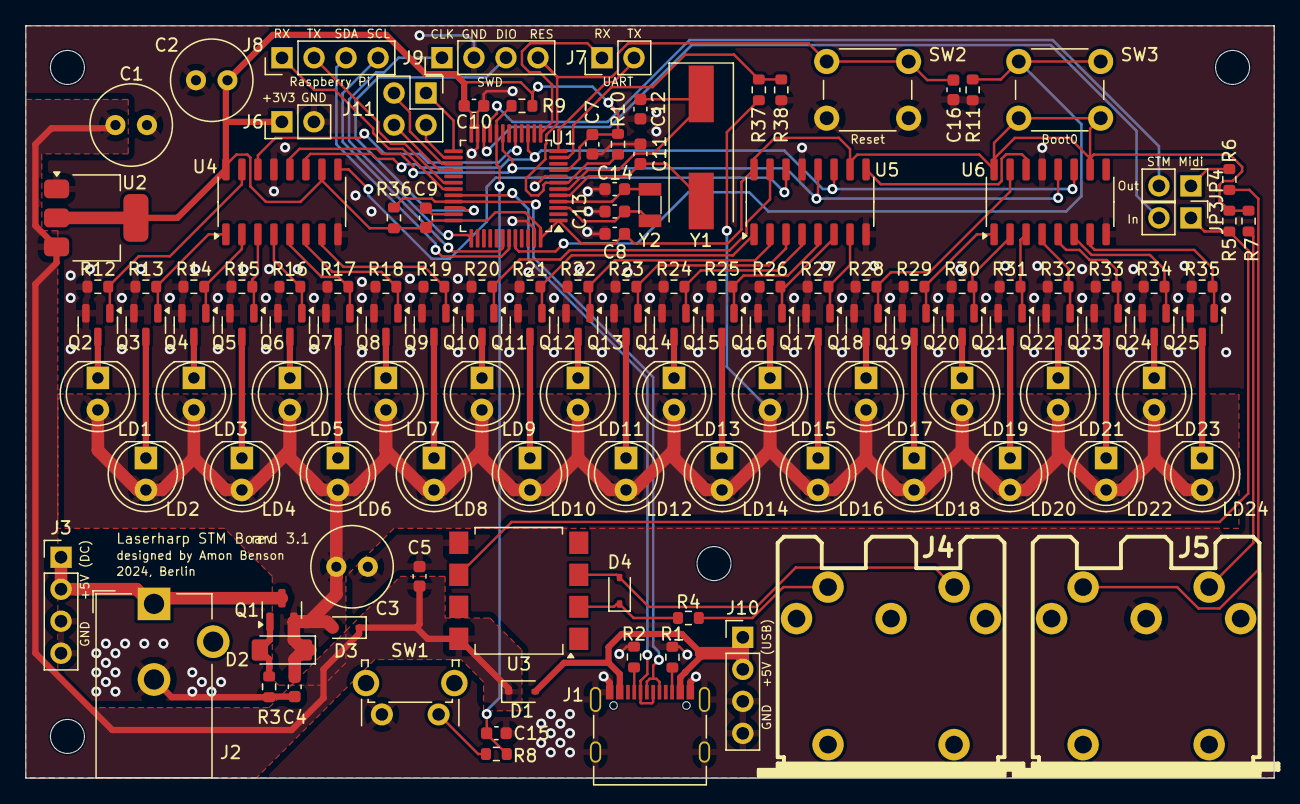
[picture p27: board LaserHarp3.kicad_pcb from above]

Board: 2 copper layers, 99.1 x 59.7 mm, 134 parts (0 on the bottom side), 94 nets.

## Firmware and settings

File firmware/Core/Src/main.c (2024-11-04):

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
/* Includes ------------------------------------------------------------------*/
#include "main.h"
#include "cmsis_os.h"
#include "usb_device.h"

/* USER CODE BEGIN Includes */
#include "animation.h"
#include "drivers/ipc.h"
#include "drivers/laser_array.h"
#include "drivers/midi_usb.h"
#include "log.h"
#include "midi_types.h"
#include "stm32f1xx_hal_adc.h"
#include "usbd_midi.h"
#include <stdbool.h>
/* USER CODE END Includes */

ADC_HandleTypeDef hadc1;

I2C_HandleTypeDef hi2c1;

SPI_HandleTypeDef hspi1;

TIM_HandleTypeDef htim2;
TIM_HandleTypeDef htim3;
DMA_HandleTypeDef hdma_tim3_ch4_up;

UART_HandleTypeDef huart1;
UART_HandleTypeDef huart2;
UART_HandleTypeDef huart3;

/* Definitions for defaultTask */
osThreadId_t defaultTaskHandle;
const osThreadAttr_t defaultTask_attributes = {
    .name = "defaultTask",
    .stack_size = 256 * 4,
    .priority = (osPriority_t) osPriorityBelowNormal,
};
/* Definitions for usbReceiveTask */
osThreadId_t usbReceiveTaskHandle;
const osThreadAttr_t usbReceiveTask_attributes = {
    .name = "usbReceiveTask",
    .stack_size = 128 * 4,
    .priority = (osPriority_t) osPriorityNormal,
};
/* Definitions for ipcReceiveTask */
osThreadId_t ipcReceiveTaskHandle;
const osThreadAttr_t ipcReceiveTask_attributes = {
    .name = "ipcReceiveTask",
    .stack_size = 128 * 4,
    .priority = (osPriority_t) osPriorityNormal,
};
/* Definitions for buttonTask */
osThreadId_t buttonTaskHandle;
const osThreadAttr_t buttonTask_attributes = {
    .name = "buttonTask",
    .stack_size = 128 * 4,
    .priority = (osPriority_t) osPriorityBelowNormal,
};
/* Definitions for usbRxData */
osMessageQueueId_t usbRxDataHandle;
const osMessageQueueAttr_t usbRxData_attributes = { .name = "usbRxData" };
/* Definitions for ipcRxData */
osMessageQueueId_t ipcRxDataHandle;
const osMessageQueueAttr_t ipcRxData_attributes = { .name = "ipcRxData" };
/* Definitions for printfSemaphore */
osSemaphoreId_t printfSemaphoreHandle;
const osSemaphoreAttr_t printfSemaphore_attributes = { .name = "printfSemaphore" };
/* Definitions for globalStatus */
osEventFlagsId_t globalStatusHandle;
const osEventFlagsAttr_t globalStatus_attributes = { .name = "globalStatus" };
/* USER CODE BEGIN PV */
laser_array_t laser_array;
animator_t animator;

uint8_t stored_brightness[LA_NUM_DIODES];
/* USER CODE END PV */

void SystemClock_Config(void);
static void MX_GPIO_Init(void);
static void MX_DMA_Init(void);
static void MX_USART1_UART_Init(void);
static void MX_USART2_UART_Init(void);
static void MX_USART3_UART_Init(void);
static void MX_SPI1_Init(void);
static void MX_TIM2_Init(void);
static void MX_TIM3_Init(void);
static void MX_I2C1_Init(void);
static void MX_ADC1_Init(void);
void StartDefaultTask(void *argument);
void StartUsbReceiveTask(void *argument);
void StartIpcReceiveTask(void *argument);
void StartButtonTask(void *argument);

/* USER CODE BEGIN PFP */
int _write(int file, char *ptr, int len);
void USBD_MIDI_DataInHandler(uint8_t *usb_rx_buffer, uint8_t usb_rx_buffer_length);
/* USER CODE END PFP */

/* USER CODE BEGIN 0 */
int _write(int file, char *ptr, int len) {
    osSemaphoreAcquire(printfSemaphoreHandle, osWaitForever);
    HAL_UART_Transmit(&huart2, (uint8_t *) ptr, len, 0xFFFF);
    osSemaphoreRelease(printfSemaphoreHandle);

    return len;
}

static bool is_btn_cal_pressed(void) {
    return HAL_GPIO_ReadPin(BTN_CAL_GPIO_Port, BTN_CAL_Pin) == GPIO_PIN_RESET;
}
#define BTN_STATES 3

// void HAL_UARTEx_RxEventCallback(UART_HandleTypeDef *huart, uint16_t Size) {
//     ipc_driver_HAL_UARTEx_RxEventCallback(huart, Size);
// }

void HAL_UART_RxCpltCallback(UART_HandleTypeDef *huart) {
    ipc_driver_HAL_UART_RxCpltCallback(huart);
}
/* USER CODE END 0 */

/**
 * @brief  The application entry point.
 * @retval int
 */
int main(void) {
    /* MCU Configuration--------------------------------------------------------*/

    /* Reset of all peripherals, Initializes the Flash interface and the Systick. */
    HAL_Init();

    /* Configure the system clock */
    SystemClock_Config();

    /* Initialize all configured peripherals */
    MX_GPIO_Init();
    MX_DMA_Init();
    MX_USART1_UART_Init();
    MX_USART2_UART_Init();
    MX_USART3_UART_Init();
    MX_SPI1_Init();
    MX_TIM2_Init();
    MX_TIM3_Init();
    MX_I2C1_Init();
    MX_ADC1_Init();
    /* Init scheduler */
    osKernelInitialize();

    /* USER CODE BEGIN RTOS_MUTEX */
    /* add mutexes, ... */
    /* USER CODE END RTOS_MUTEX */

    /* Create the semaphores(s) */
    /* creation of printfSemaphore */
    printfSemaphoreHandle = osSemaphoreNew(1, 0, &printfSemaphore_attributes);

    /* USER CODE BEGIN RTOS_SEMAPHORES */
    osSemaphoreRelease(printfSemaphoreHandle);
    /* USER CODE END RTOS_SEMAPHORES */

    /* USER CODE BEGIN RTOS_TIMERS */
    /* start timers, add new ones, ... */
    /* USER CODE END RTOS_TIMERS */

    /* Create the queue(s) */
    /* creation of usbRxData */
    usbRxDataHandle = osMessageQueueNew(32, sizeof(midi_packet_t), &usbRxData_attributes);

    /* creation of ipcRxData */
    ipcRxDataHandle = osMessageQueueNew(32, sizeof(ipc_packet_t), &ipcRxData_attributes);

    /* USER CODE BEGIN RTOS_QUEUES */
    /* add queues, ... */
    /* USER CODE END RTOS_QUEUES */

    /* Create the thread(s) */
    /* creation of defaultTask */
    defaultTaskHandle = osThreadNew(StartDefaultTask, NULL, &defaultTask_attributes);

    /* creation of usbReceiveTask */
    usbReceiveTaskHandle = osThreadNew(StartUsbReceiveTask, NULL, &usbReceiveTask_attributes);

    /* creation of ipcReceiveTask */
    ipcReceiveTaskHandle = osThreadNew(StartIpcReceiveTask, NULL, &ipcReceiveTask_attributes);

    /* creation of buttonTask */
    buttonTaskHandle = osThreadNew(StartButtonTask, NULL, &buttonTask_attributes);

    /* USER CODE BEGIN RTOS_THREADS */
    /* add threads, ... */
    /* USER CODE END RTOS_THREADS */

    /* Create the event(s) */
    /* creation of globalStatus */
    globalStatusHandle = osEventFlagsNew(&globalStatus_attributes);

    /* USER CODE BEGIN RTOS_EVENTS */

    // initialize drivers
    midi_usb_driver_init(usbRxDataHandle);
    ipc_driver_init(&huart1, ipcRxDataHandle);

    const laser_array_config_t laser_array_config = {
        .hspi = &hspi1,
        .htim_transfer = &htim3,
        .htim_fade = &htim2,
        .rclk_channel = TIM_CHANNEL_4,
    };
    laser_array_init(&laser_array, &laser_array_config);

    // initialize animator (note: the boot animation is started in the default task)
    const animator_config_t animator_config = {
        .laser_array = &laser_array,
    };
    animator_init(&animator, &animator_config);
    /* USER CODE END RTOS_EVENTS */

    /* Start scheduler */
    osKernelStart();

    /* We should never get here as control is now taken by the scheduler */
    /* Infinite loop */
    /* USER CODE BEGIN WHILE */
    while (1) {
        /* USER CODE END WHILE */

        /* USER CODE BEGIN 3 */
    }
    /* USER CODE END 3 */
}

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
/* USER CODE BEGIN Header_StartDefaultTask */
/**
 * @brief  Function implementing the defaultTask thread.
 * @param  argument: Not used
 * @retval None
 */
/* USER CODE END Header_StartDefaultTask */
void StartDefaultTask(void *argument) {
    /* init code for USB_DEVICE */
    MX_USB_DEVICE_Init();
    /* USER CODE BEGIN 5 */

    printf("\n\n\n");
    LOG_INFO("Laserharp Firmware version %s", FIRMWARE_VERSION_STR);
    LOG_INFO("Created by Amon Benson");
    LOG_INFO("Compiled on %s at %s", __DATE__, __TIME__);

    // enable all lasers on startup
    for (uint8_t i = 0; i < LA_NUM_DIODES; i++) {
        laser_array_set_brightness(&laser_array, i, LA_NUM_BRIGHTNESS_LEVELS - 1);
    }

    // play the boot animation
    animator_play(&animator, ANIMATION_BOOT, ANIMATION_BOOT_SPEED, ANIMATION_LOOP);

    for (;;) {
        // update the animator. Assume a fixed time step of 20ms
        animator_update(&animator, 0.02);

        // check if we need to restore the stored brightness values. This will happen at the end of an animation if the
        // follow_action was set to ANIMATION_STOP_RESTORE
        if (animator_is_restore_required(&animator)) {
            for (uint8_t i = 0; i < LA_NUM_DIODES; i++) {
                laser_array_set_brightness(&laser_array, i, stored_brightness[i]);
            }
        }

        osDelay(20);
    }
    /* USER CODE END 5 */
}

/* USER CODE BEGIN Header_StartUsbReceiveTask */
/**
 * @brief Function implementing the usbReceiveTask thread.
 * @param argument: Not used
 * @retval None
 */
/* USER CODE END Header_StartUsbReceiveTask */
void StartUsbReceiveTask(void *argument) {
    /* USER CODE BEGIN StartUsbReceiveTask */
    midi_packet_t packet;

    for (;;) {
        // wait for a packet to be received
        if (osMessageQueueGet(usbRxDataHandle, &packet, NULL, osWaitForever) != osOK) {
            LOG_ERROR("USB MIDI: Failed to get packet from usbRxData");
            continue;
        }

        // print the received packet
        LOG_TRACE("USB MIDI: Received packet: " MIDI_PACKET_FMT, MIDI_PACKET_FMT_ARGS(&packet));

        // forward the midi packet to the Raspberry Pi
        ipc_packet_t ipc_packet = { 0 };
        ipc_packet[0] = packet.cn_cin & 0xf0; // force cable number to 0
        ipc_packet[1] = packet.status;
        ipc_packet[2] = packet.data1;
        ipc_packet[3] = packet.data2;
        ipc_driver_transmit(&ipc_packet);
    }
    /* USER CODE END StartUsbReceiveTask */
}

/* USER CODE BEGIN Header_StartIpcReceiveTask */
static uint8_t ipc_velocity_to_brightness(uint8_t velocity) {
    return (uint8_t) ((uint32_t) velocity * (LA_NUM_BRIGHTNESS_LEVELS - 1) / 127);
}

static uint8_t ipc_brightness_to_velocity(uint8_t brightness) {
    return (uint8_t) ((uint32_t) brightness * 127 / (LA_NUM_BRIGHTNESS_LEVELS - 1));
}

/**
 * @brief Function implementing the ipcReceiveTask thread.
 * @param argument: Not used
 * @retval None
 */
/* USER CODE END Header_StartIpcReceiveTask */
void StartIpcReceiveTask(void *argument) {
    /* USER CODE BEGIN StartIpcReceiveTask */
    ipc_packet_t packet, response;

    for (;;) {
        // wait for a packet to be received
        if (osMessageQueueGet(ipcRxDataHandle, &packet, NULL, osWaitForever) != osOK) {
            LOG_ERROR("IPC: Failed to get packet from ipcRxData");
            continue;
        }

        // print the received packet
        LOG_TRACE("IPC: Received packet: " IPC_PACKET_FMT, IPC_PACKET_FMT_ARGS(&packet));

        // stop the intro animation when the first IPC packet is received
        if (animator_get_current_animation(&animator) == ANIMATION_BOOT && animator_is_playing(&animator)) {
            animator_stop(&animator);
        }

        uint8_t major_code = packet[0] & 0xF0;
        uint8_t code = packet[0];

        // initialize response
        response[0] = code;
        response[1] = 0;
        response[2] = 0;
        response[3] = 0;

        switch (major_code) {
            case 0x00: // forward USB midi out packet
                LOG_WARN("IPC: USB Midi Out not implemented");
                break;
            case 0x10: // forward DIN midi out packet
                LOG_WARN("IPC: Din Midi Out not implemented");
                break;
            default: // check full code
                switch (code) {
                    case 0x80: // set brightness of a single laser
                        LOG_DEBUG("IPC: Set brightness of laser %d", packet[1]);

                        // validate the parameters
                        if (packet[1] >= LA_NUM_DIODES) {
                            LOG_ERROR("IPC: Invalid laser number %d", packet[1]);
                            break;
                        }
                        if (packet[2] > 127) {
                            LOG_ERROR("IPC: Invalid brightness %d", packet[2]);
                            break;
                        }

                        // update the laser diode only if the animator is not playing
                        if (!animator_is_playing(&animator)) {
                            if (packet[3] == 0) {
                                laser_array_set_brightness(
                                    &laser_array, packet[1], ipc_velocity_to_brightness(packet[2]));
                            } else {
                                laser_array_fade_brightness(&laser_array, packet[1],
                                    ipc_velocity_to_brightness(packet[2]), (uint32_t) packet[3] * 100);
                            }
                        }

                        // store the brightness value
                        stored_brightness[packet[1]] = packet[2];
                        break;
                    case 0x81: // set brightness of multiple lasers
                        LOG_DEBUG("IPC: Set brightness of all lasers");

                        // validate the parameters
                        if (packet[1] > 127) {
                            LOG_ERROR("IPC: Invalid brightness %d", packet[1]);
                            break;
                        }

                        // update all laser diodes at once. Again, skip if the animator is playing
                        for (uint8_t i = 0; i < LA_NUM_DIODES; i++) {
                            if (!animator_is_playing(&animator)) {
                                if (packet[2] == 0) {
                                    laser_array_set_brightness(&laser_array, i, ipc_velocity_to_brightness(packet[1]));
                                } else {
                                    laser_array_fade_brightness(&laser_array, i, ipc_velocity_to_brightness(packet[1]),
                                        (uint32_t) packet[2] * 100);
                                }
                            }

                            stored_brightness[i] = packet[1];
                        }
                        break;
                    case 0x82: // get brightness of a single laser
                        LOG_DEBUG("IPC: Get brightness of laser %d", packet[1]);
                        response[1] = packet[1];
                        response[2] = ipc_brightness_to_velocity(laser_array_get_brightness(&laser_array, packet[1]));
                        ipc_driver_transmit(&response);
                        break;
                    case 0x83: // play animation
                        LOG_DEBUG("IPC: Play animation %d", packet[1]);
                        animator_play(&animator, packet[1], packet[2] * 0.1f, packet[3]);
                        break;
                    case 0x84: // stop animation
                        LOG_DEBUG("IPC: Stop animation");
                        animator_stop(&animator);
                        break;
                    case 0x91: // get voltage
                        LOG_DEBUG("IPC: Get voltage");
                        if (packet[1] == 0) {
                            // poll the ADC for a voltage. This will not run very often, so blocking is fine
                            HAL_ADCEx_Calibration_Start(&hadc1);
                            HAL_ADC_Start(&hadc1);

                            HAL_ADC_PollForConversion(&hadc1, HAL_MAX_DELAY);
                            uint32_t measurement_raw = HAL_ADC_GetValue(&hadc1);

                            HAL_ADC_Stop(&hadc1);

                            float measurement_voltage = measurement_raw * 3.3f / 4095;
                            float converted_voltage = measurement_voltage * (220 + 330) / 330; // voltage divider

                            response[2] = (uint8_t) converted_voltage;
                            response[3] = (uint8_t) ((converted_voltage - response[2]) * 100);
                        } else {
                            // currently only one voltage can be measured
                            response[2] = 0;
                            response[3] = 0;
                        }
                        ipc_driver_transmit(&response);
                    case 0xf0: // firmware version inquiry
                        LOG_DEBUG("IPC: Firmware version inquiry");
                        response[1] = FIRMWARE_VERSION_MAJOR;
                        response[2] = FIRMWARE_VERSION_MINOR;
                        response[3] = FIRMWARE_VERSION_PATCH;
                        ipc_driver_transmit(&response);
                        break;
                    case 0xf1: // reboot
                        LOG_INFO("IPC: Rebooting");
                        NVIC_SystemReset();
                        break;
                    case 0xf2: // enter standby
                        LOG_INFO("IPC: Entering standby");

                        // play the boot animation
                        animator_play(&animator, ANIMATION_BOOT, ANIMATION_BOOT_SPEED, ANIMATION_LOOP);

                        // sleep for the specified delay
                        osDelay(packet[1] * 100);

                        // fade all lasers to zero brightness
                        animator_stop(&animator);
                        for (uint8_t i = 0; i < LA_NUM_DIODES; i++) {
                            laser_array_fade_brightness(&laser_array, i, 0, (uint32_t) packet[2] * 100);
                        }

                        // wait until the fade is complete
                        osDelay(packet[2] * 100 + 100);

                        // enter standby mode
                        // __HAL_PWR_CLEAR_FLAG(PWR_FLAG_WU); // clear the wake-up flag
                        // HAL_PWR_EnterSTANDBYMode(); // enter standby mode
                        // while (1) { } // should never reach here

                        // clear the ipcRxData queue so that messages received during standby are not processed
                        osMessageQueueReset(ipcRxDataHandle);

                        break;
                    default:
                        LOG_ERROR("IPC: Unknown command %02X", code);
                        break;
                }
        }
    }
    /* USER CODE END StartIpcReceiveTask */
}

/* USER CODE BEGIN Header_StartButtonTask */
/**
 * @brief Function implementing the buttonTask thread.
 * @param argument: Not used
 * @retval None
 */
/* USER CODE END Header_StartButtonTask */
void StartButtonTask(void *argument) {
    /* USER CODE BEGIN StartButtonTask */
    uint32_t num_states = 3;
    uint8_t btn_pattern[3];

    /* Infinite loop */
    for (;;) {
        // reset the button pattern
        for (uint32_t i = 0; i < num_states; i++) {
            btn_pattern[i] = 'X';
        }

        for (uint32_t i = 0; i < num_states; i++) {
            // wait until button is pressed
            while (!is_btn_cal_pressed()) {
                osDelay(20);
            }

            // wait if the button gets released within the duration of a short press
            bool released = false;
            for (int i = 0; i < BTN_CAL_SHORT_PRESS_DURATION / 20; i++) {
                osDelay(20);
                if (!is_btn_cal_pressed()) {
                    released = true;
                    break;
                }
            }

            // register the button press
            if (released) {
                btn_pattern[i] = 'S';
            } else {
                btn_pattern[i] = 'L';

                // // wait until the button is released
                // while (is_btn_cal_pressed()) {
                //     osDelay(20);
                // }

                // break the outer loop as a long press ends the sequence
                break;
            }

            // check if the button gets pressed again within the duration of a short press
            bool pressed_again = false;
            for (int i = 0; i < BTN_CAL_SHORT_PRESS_DURATION / 20; i++) {
                osDelay(20);
                if (is_btn_cal_pressed()) {
                    pressed_again = true;
                    break;
                }
            }

            // if the button was not pressed again, break the outer loop
            if (!pressed_again) {
                break;
            }
        }

        // send the button pattern to the ipc
        LOG_TRACE("Button pattern: %d %d %d", btn_pattern[0], btn_pattern[1], btn_pattern[2]);
        ipc_packet_t packet = { 0 };
        packet[0] = 0x90;
        packet[1] = btn_pattern[0];
        packet[2] = btn_pattern[1];
        packet[3] = btn_pattern[2];
        ipc_driver_transmit(&packet);

        // wait until button is released for at least the duration of a short press
        bool released = false;
        int i = 0;
        while (!released) {
            osDelay(20);

            if (!is_btn_cal_pressed()) {
                i++;
            } else {
                i = 0;
            }

            if (i >= BTN_CAL_SHORT_PRESS_DURATION / 20) {
                released = true;
            }
        }
    }
    /* USER CODE END StartButtonTask */
}

/**
 * @brief  Period elapsed callback in non blocking mode
 * @note   This function is called  when TIM1 interrupt took place, inside
 * HAL_TIM_IRQHandler(). It makes a direct call to HAL_IncTick() to increment
 * a global variable "uwTick" used as application time base.
 * @param  htim : TIM handle
 * @retval None
 */
void HAL_TIM_PeriodElapsedCallback(TIM_HandleTypeDef *htim) {
    if (htim->Instance == TIM1) {
        HAL_IncTick();
    }
    /* USER CODE BEGIN Callback 1 */
    if (htim->Instance == laser_array.config.htim_fade->Instance) {
        laser_array_fade_TIM_PeriodElapsedHandler(&laser_array);
    }
    /* USER CODE END Callback 1 */
}

/**
 * @brief  This function is executed in case of error occurrence.
 * @retval None
 */
void Error_Handler(void) {
    /* USER CODE BEGIN Error_Handler_Debug */
    /* User can add his own implementation to report the HAL error return state */
    __disable_irq();
    while (1) { }
    /* USER CODE END Error_Handler_Debug */
}
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

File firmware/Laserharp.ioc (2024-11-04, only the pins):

Mcu.UserName=STM32F103C8Tx
PA1.GPIO_Label=LA_VPROBE
PA1.Signal=ADCx_IN1
PA10.GPIO_Label=IPC_RX
PA10.Signal=USART1_RX
PA11.Signal=USB_DM
PA12.Signal=USB_DP
PA13.Signal=SYS_JTMS-SWDIO
PA14.Signal=SYS_JTCK-SWCLK
PA2.GPIO_Label=DEBUG_TX
PA2.Signal=USART2_TX
PA3.GPIO_Label=DEBUG_RX
PA3.Signal=USART2_RX
PA5.GPIO_Label=LA_CLK
PA5.Signal=SPI1_SCK
PA7.GPIO_Label=LA_DS
PA7.Signal=SPI1_MOSI
PA9.GPIO_Label=IPC_TX
PA9.Signal=USART1_TX
PB1.GPIO_Label=LA_LATCH
PB1.Signal=S_TIM3_CH4
PB10.GPIO_Label=DIN_TX
PB10.Signal=USART3_TX
PB11.GPIO_Label=DIN_RX
PB11.Signal=USART3_RX
PB2.GPIO_Label=BTN_CAL
PB2.Signal=GPIO_Input
PB6.GPIO_Label=IPC_SCL
PB6.Signal=I2C1_SCL
PB7.GPIO_Label=IPC_SDA
PB7.Signal=I2C1_SDA
PD0-OSC_IN.Signal=RCC_OSC_IN
PD1-OSC_OUT.Signal=RCC_OSC_OUT

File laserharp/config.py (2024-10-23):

import os
import logging
import yaml


DEFAULT_CONFIG_FILENAME = os.path.abspath(os.path.join(os.path.dirname(__file__), "config.yaml"))


def load_config(filename: str = None, config_logging: bool = True, verbose_logging: bool = False):
    if filename is None:
        filename = DEFAULT_CONFIG_FILENAME

    if not os.path.exists(filename):
        raise FileNotFoundError(f"Config file not found at: {filename}")

    # load the configuration
    with open(filename, "r", encoding="utf-8") as f:
        _config = yaml.safe_load(f)

    # configure logging
    if config_logging:
        logging.basicConfig(
            level=_config["app"]["log_level"] if not verbose_logging else "DEBUG",
            format="%(asctime)s %(levelname)s %(pathname)s: %(message)s",
        )

    return _config


if __name__ == "__main__":
    import json

    config = load_config()

    print("Confguration:")
    print(json.dumps(config, indent=2))

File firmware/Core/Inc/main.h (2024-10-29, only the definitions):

#define FIRMWARE_VERSION_MAJOR 0
#define FIRMWARE_VERSION_MINOR 1
#define FIRMWARE_VERSION_PATCH 0
#define FIRMWARE_VERSION_STR \
#define MIDI_IN_PORTS_NUM 0x01 // Specify input ports number of your device
#define MIDI_OUT_PORTS_NUM 0x01 // Specify output ports number of your device
#define HUART_DEBUG huart2
#define HUART_DIN huart3
#define LA_TRANSFER_PRESCALAR 128
#define HUART_IPC huart1
#define LA_FADE_TICK_RATE 30
#define LA_VPROBE_Pin GPIO_PIN_1
#define LA_VPROBE_GPIO_Port GPIOA
#define DEBUG_TX_Pin GPIO_PIN_2
#define DEBUG_TX_GPIO_Port GPIOA
#define DEBUG_RX_Pin GPIO_PIN_3
#define DEBUG_RX_GPIO_Port GPIOA
#define LA_CLK_Pin GPIO_PIN_5
#define LA_CLK_GPIO_Port GPIOA
#define LA_DS_Pin GPIO_PIN_7
#define LA_DS_GPIO_Port GPIOA
#define LA_LATCH_Pin GPIO_PIN_1
#define LA_LATCH_GPIO_Port GPIOB
#define BTN_CAL_Pin GPIO_PIN_2
#define BTN_CAL_GPIO_Port GPIOB
#define DIN_TX_Pin GPIO_PIN_10
#define DIN_TX_GPIO_Port GPIOB
#define DIN_RX_Pin GPIO_PIN_11
#define DIN_RX_GPIO_Port GPIOB
#define IPC_TX_Pin GPIO_PIN_9
#define IPC_TX_GPIO_Port GPIOA
#define IPC_RX_Pin GPIO_PIN_10
#define IPC_RX_GPIO_Port GPIOA
#define IPC_SCL_Pin GPIO_PIN_6
#define IPC_SCL_GPIO_Port GPIOB
#define IPC_SDA_Pin GPIO_PIN_7
#define IPC_SDA_GPIO_Port GPIOB
#define BTN_CAL_SHORT_PRESS_DURATION 500
#define ANIMATION_BOOT_SPEED 5.0f

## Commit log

2023-10-04 added camera test
2023-10-04 added better camera processing
2023-10-05 added calibration visualization
2023-10-06 basic processing loop (cam->midi_out->midi_in->lasers) working
2023-10-11 massive performance improve by using threads
2023-10-18 added actual calibration code
2023-10-23 added better calibration sequence, data gets stored to json file
2023-10-24 added new calibration format
2023-10-24 sync with main thread now working
2023-10-25 bugfixes with the new config system
    [__main__.py, app.py, camera.py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]
2023-10-25 added pitch bend functionality
2023-10-26 added laser array, changes to test suite
2023-10-28 added and tested laser array
2023-10-28 large rework of class system
    [image_processor.py, laser_array.py]
2023-10-28 major update to camera, untested
2023-10-29 reworked camera module
2023-10-29 added invalid cable test
2023-10-29 added new calibrator class with tests
2023-10-29 added flag for calibrator debug images
2023-10-29 added load and save functionality to calibrator
2024-08-14 validated working camera
2024-08-14 made camera tests optional
2024-08-14 added custom camera output stream handler
2024-08-18 added frontend camera stream
2024-08-19 updated state management on server, fixed bug in beam visualization
    [events.py, image_calibrator.py, image_processor.py]
2024-09-04 added hardware files
    [3dp_parts.3mf, BOM-Laserharp_Panels.csv, Bottom Plate.3mf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]
2024-09-04 added stm files
    [stm32f1x-bluepill.cfg]
2024-09-09 added MIDI usb driver
2024-09-10 moved usb code to separate driver
2024-09-10 added ipc driver
2024-09-10 added laserarray
2024-09-11 updated calibration process
2024-09-15 added more laser diodes, added calibrate button to web ui
2024-09-16 fixed testing framework
2024-09-16 fixed a lot of linting issues
    [app.py, camera.py, image_calibrator.py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]
2024-09-17 added new config to laser_array
2024-09-17 added new config system to camera
2024-09-17 added image calibration state
2024-09-18 updated camera to include a frame tracker
2024-09-18 added new calibration view
2024-09-18 added calibration live view
2024-09-18 fixed issues with calibration
    [app.py]
2024-09-22 added section on gpio power
2024-09-22 updates to vscode startup settings and camera view
2024-09-22 added settings, fixes in backend and frontend
    [config.yaml, din_midi.py, ipc.py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]
2024-09-22 upped camera frame rate to 50 FPS
2024-09-24 renamed directories
    [3dp_parts.3mf, BOM-Laserharp_Panels.csv, Bottom Plate.3mf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]
2024-09-28 calibration is now stored in the settings file
2024-09-29 fixed initial laser brightness
    [app.py, midi_converter.py]
2024-09-29 fixed bug in image processor
    [config.yaml, image_processor.py]
2024-10-03 fixed laserharp service
2024-10-12 added uart check and some bugfixes
    [config.yaml, store.py]
2024-10-12 added camera fixes for raspberry pi 3
    [camera.py, config.yaml]
2024-10-15 updates config and home view to work with raspberry pi 5
2024-10-15 updated pcb
    [BOM-LaserHarp3.csv, LaserHarp3.dsn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]
2024-10-15 updated laser brightness in intro animation
2024-10-20 fixed image calibrator tests
2024-10-21 added first fabrication order export
    [BOM-Laserharp_Panels.csv, Engravings.dxf, LH_All.dxf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]
2024-10-23 small bugfixes, persisting mjpeg stream issue in firefox
    [__main__.py, camera.py, config.py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]
2024-10-27 added calibration button and voltage specs to readme
2024-10-28 added restore follow_action and updated the flip animation
    [main.c]
2024-10-28 added flip animation trigger
    [laser_array.py, orchestrator.py]
2024-10-29 implemented laser fading via ipc command
2024-10-29 added tests for laser fading, added fade during startup
2024-10-29 added calibration button to firmware
2024-10-29 implemented calibration and poweroff button
2024-10-30 updates to standby and cal button
2024-10-30 changed non-button sequence character
2024-10-30 hwbutton working, fixed bug where lasers wouldn't turn off at the start of a calibration
    [app.py, config.yaml, hwbutton.py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]
2024-10-30 added button assignment and quick actions to frontend
2024-11-04 removed old hw folder
    [BOM-LaserHarp3.csv, LaserHarp3.dsn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]
2024-11-04 added get voltage function
2024-11-07 implemented direct laser control via DIN midi
2024-11-11 fixed camera streaming issues
    [camera.py, config.yaml]
2024-11-20 added jlc3dp ordered parts
    [3dp_parts.3mf, CameraCabinet.3mf, CameraMount.3mf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]
2025-05-15 updates to mount angle etc.
2025-05-26 fixed calibration issues
2025-05-28 added oversampling thread without functionality
2025-05-28 added flipping for the new orchestrator
    [orchestrator.py]
2025-05-28 added more frame blurring to smooth out beam length
2025-05-28 added kalman filter for camera pixel input
2025-05-28 fixed bug with emulated beam brightness
    [orchestrator.py]
2025-06-04 implemented calibration using 2nd order polynom
2025-06-04 fixed bug in calibration and updated configured coverage
    [config.yaml, image_calibrator.py]
2025-06-26 updated lens mount, added midi sheet
    [Lens Mount.3mf, LensMount.3mf, Midi_Cheat_Sheet.xlsx]

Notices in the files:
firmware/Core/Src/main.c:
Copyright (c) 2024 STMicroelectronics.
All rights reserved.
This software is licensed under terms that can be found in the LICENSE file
